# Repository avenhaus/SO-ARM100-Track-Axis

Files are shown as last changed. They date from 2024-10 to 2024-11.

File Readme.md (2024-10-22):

# <center>SO-ARM100 Track Axis</center>

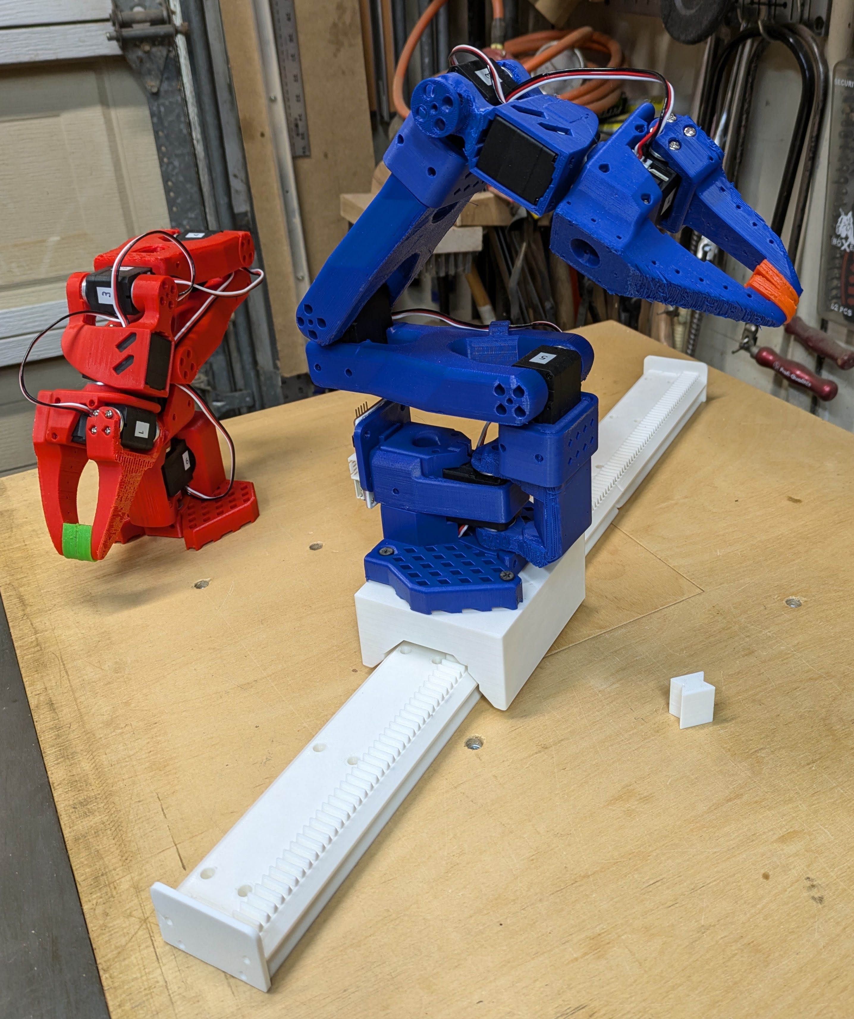
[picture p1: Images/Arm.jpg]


## Summary
This project is related to the [SO-ARM100](https://github.com/TheRobotStudio/SO-ARM100) robot arm and [LeRobot](https://github.com/huggingface/lerobot)

It provides an additional axis, using the same STS3215 servo.

The carriage comes in 2 Versions:
1) Direct Drive (best for leader with [encoders](https://github.com/avenhaus/SO-ARM100-Encoders) or higher precision)
2) Additional gear for twice the speed

## Hardware

- 1 x FeeTech STS3215 Servo (same as SO-ARM100)
- 8 x 624 Bearing (ID: 4mm / OD: 13mm / H: 5mm)
- 8 x M4 10mm or 12mm machine screws for bearings
- 6 x M3 6mm or 8mm screws for motor bracket
- 4 x M4 20mm bolts and hex nuts to mount arm to slide (there are also versions with 3.2mm holes for drywall screws)
- M3 wood screws to mount rails to wooden base

The "Fast" version with additional gear additionally needs: 
- 2 x 624 Bearing (ID: 4mm / OD: 13mm / H: 5mm)
- 1 x 4mm rod, ca. 35mm, longer is fine

### Drive Gear Specs

- Modulo: 1.5
- Pressure Angle: 20
- 18 Teeth
- Height: 14mm 

## Code

The servo can give current feedback. This is used to home the axis and find the length of the track. A small python program demonstrates this and also shows how to keep track of multiple servo rotations.

- Find end of track
- Find home position
- Move to 10% and 90% of track length
- Move to middle

## Video

**https://youtu.be/PuqxYcexV3M**

## Images

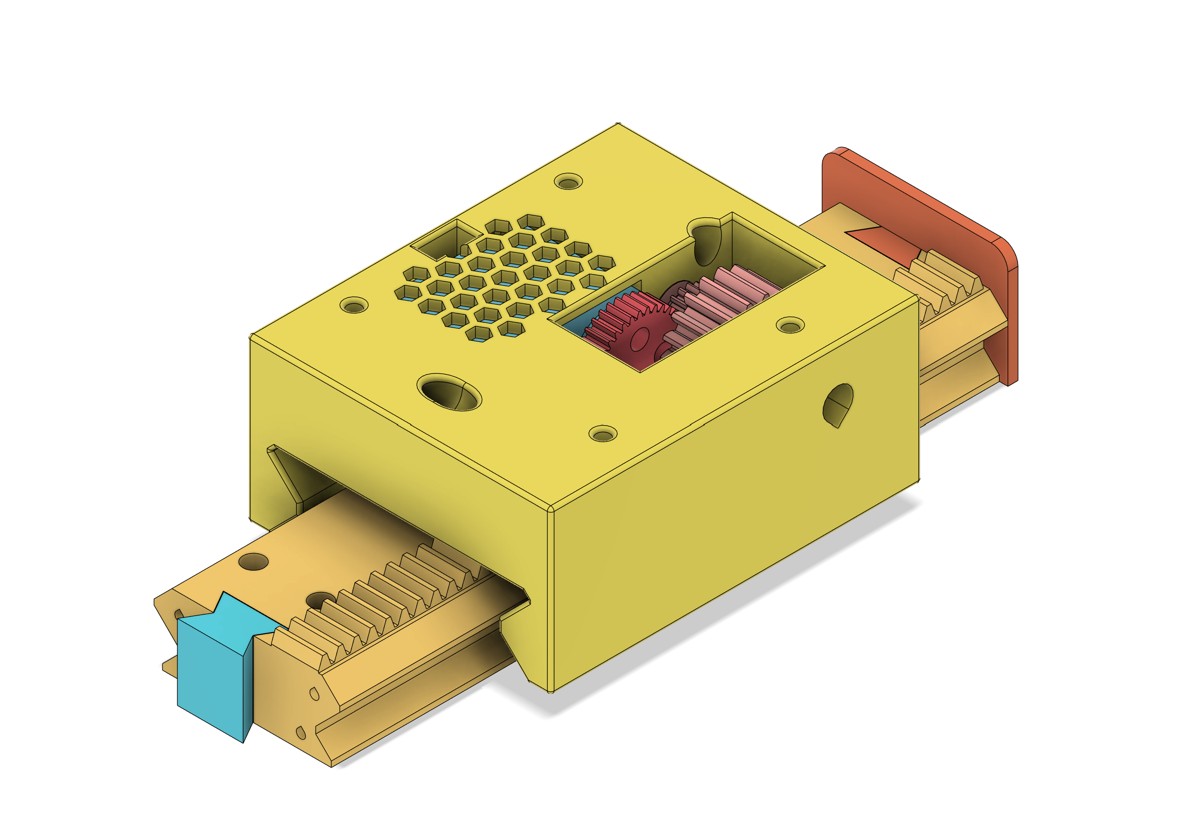
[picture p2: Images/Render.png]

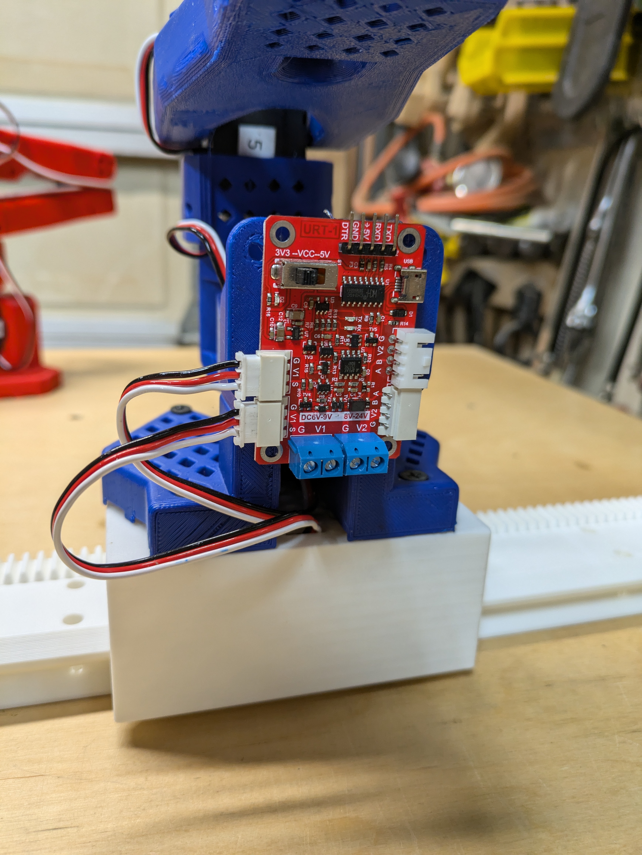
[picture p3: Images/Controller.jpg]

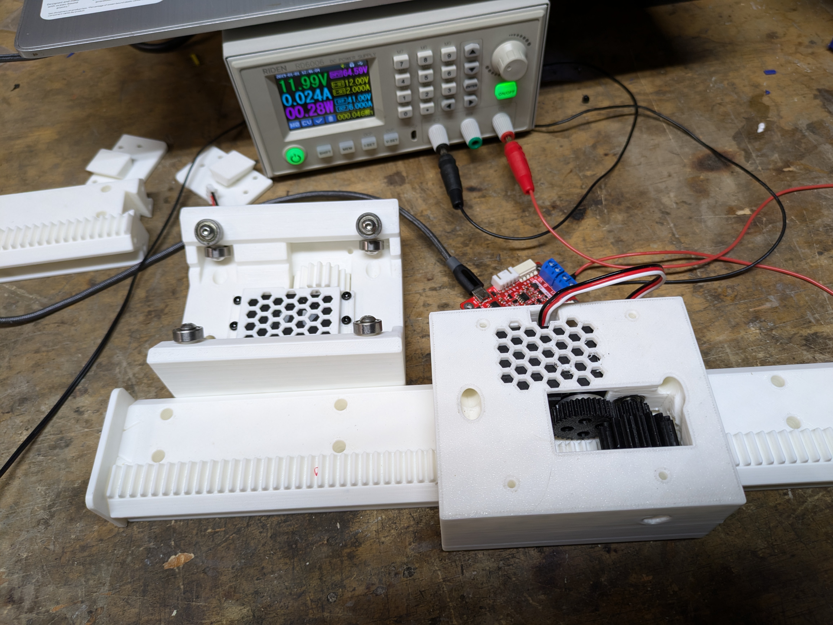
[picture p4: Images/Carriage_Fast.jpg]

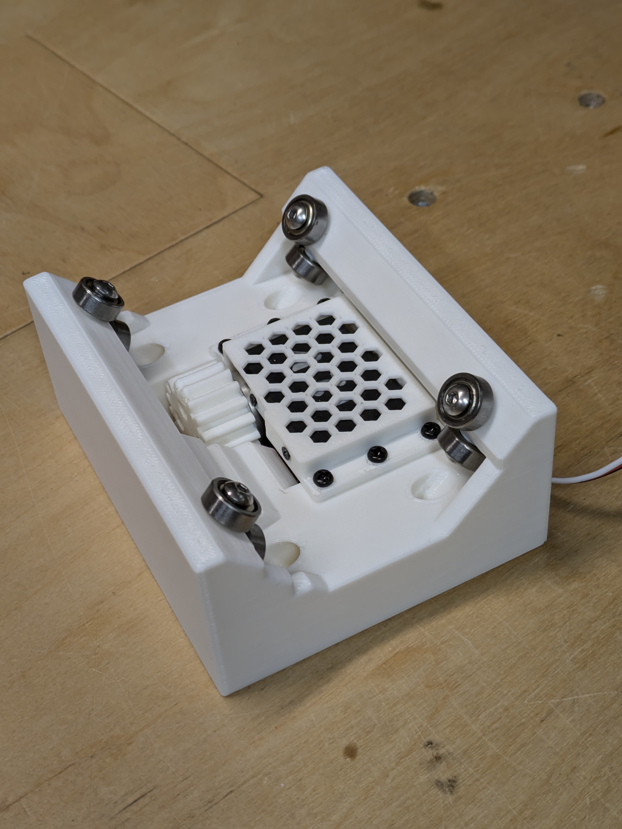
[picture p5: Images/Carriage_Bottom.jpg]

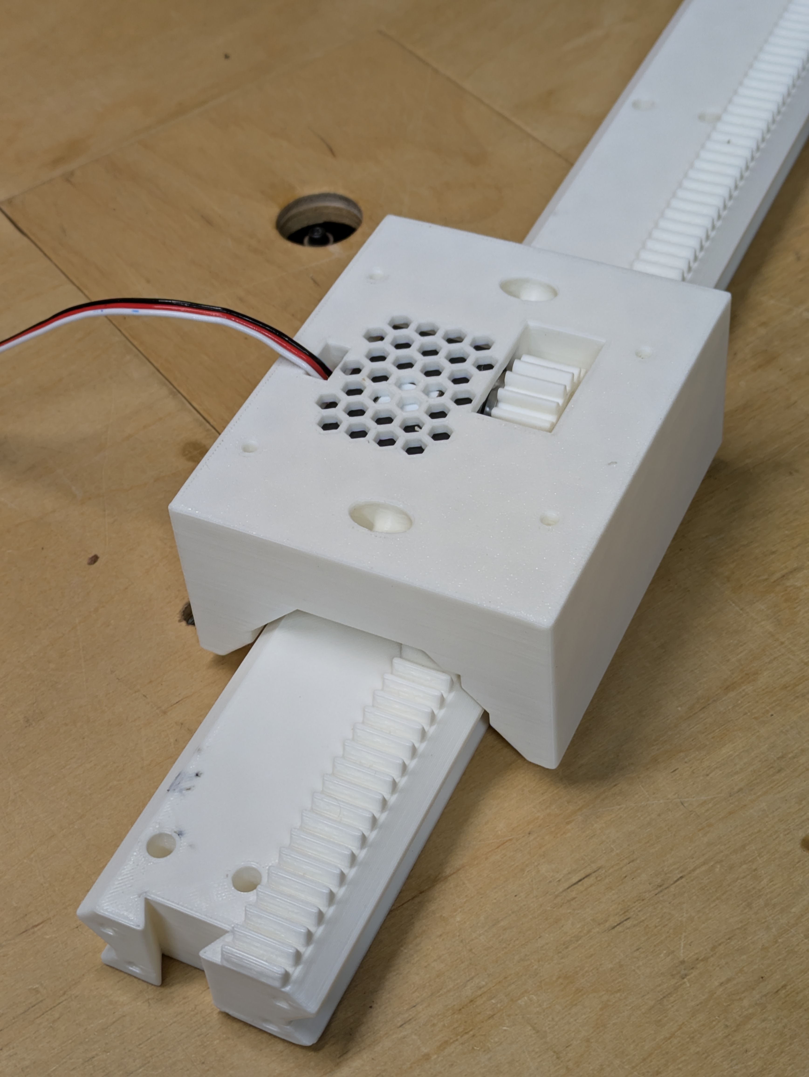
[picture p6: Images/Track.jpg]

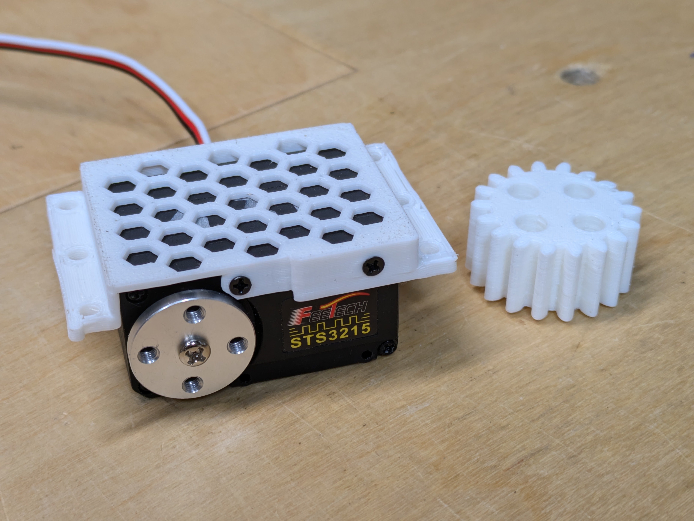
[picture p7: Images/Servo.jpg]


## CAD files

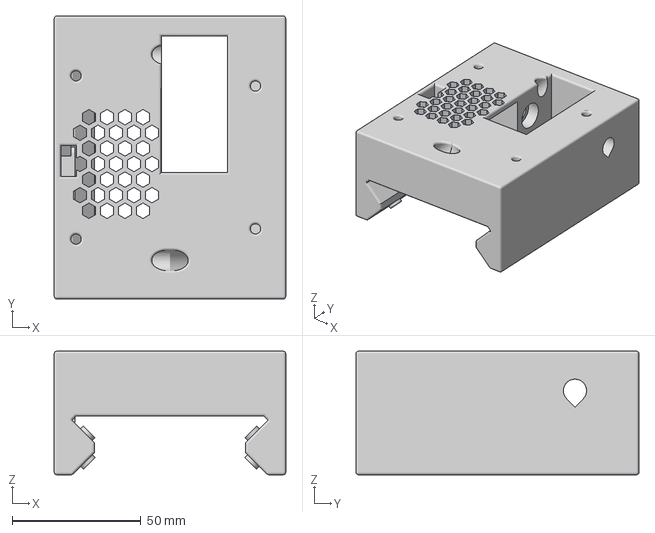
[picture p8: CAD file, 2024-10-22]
Parts/Carriage Fast M4 Mounts.3mf
90.0 x 110.0 x 48.0 mm

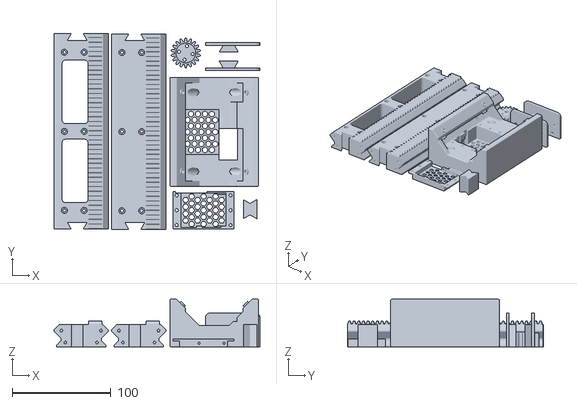
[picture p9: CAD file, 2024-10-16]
SO-ARM100_7th_Axis.stl
208.4 x 198.3 x 48.0

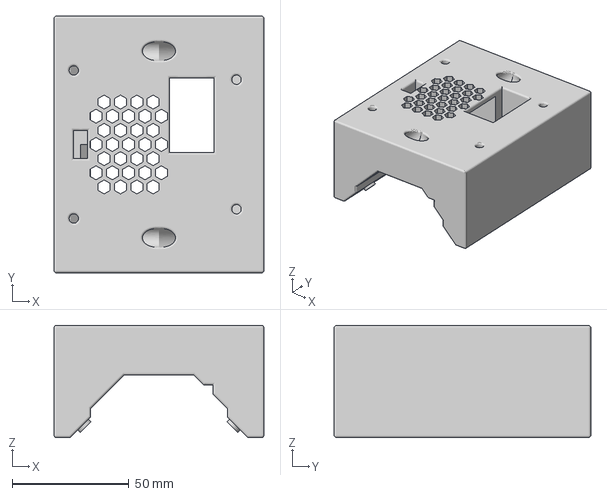
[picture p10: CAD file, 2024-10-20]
Parts/Carriage Slow M4 Mounts.3mf
90.0 x 110.0 x 48.0 mm

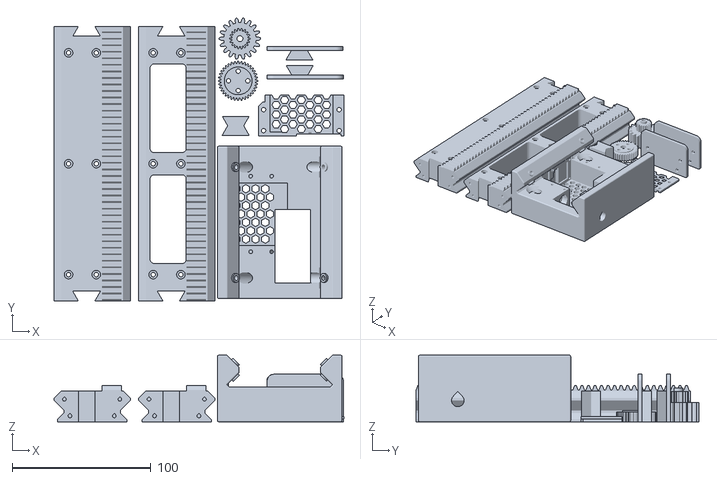
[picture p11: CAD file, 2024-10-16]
SO-ARM100_7th_Axis_Fast.stl
209.2 x 204.0 x 48.0

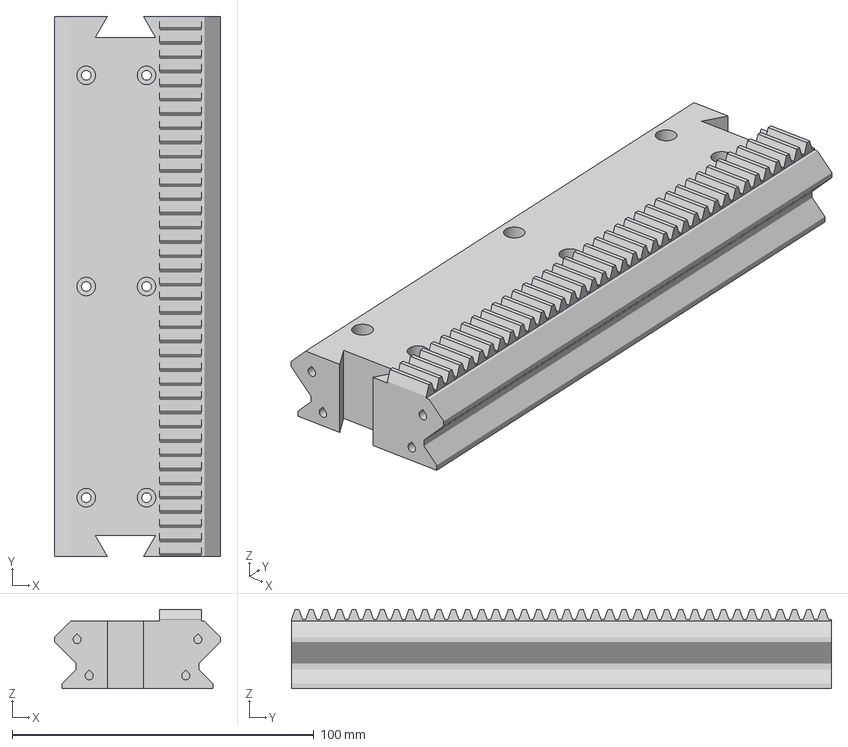
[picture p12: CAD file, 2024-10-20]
Parts/Track 179mm.3mf
55.0 x 179.1 x 26.2 mm

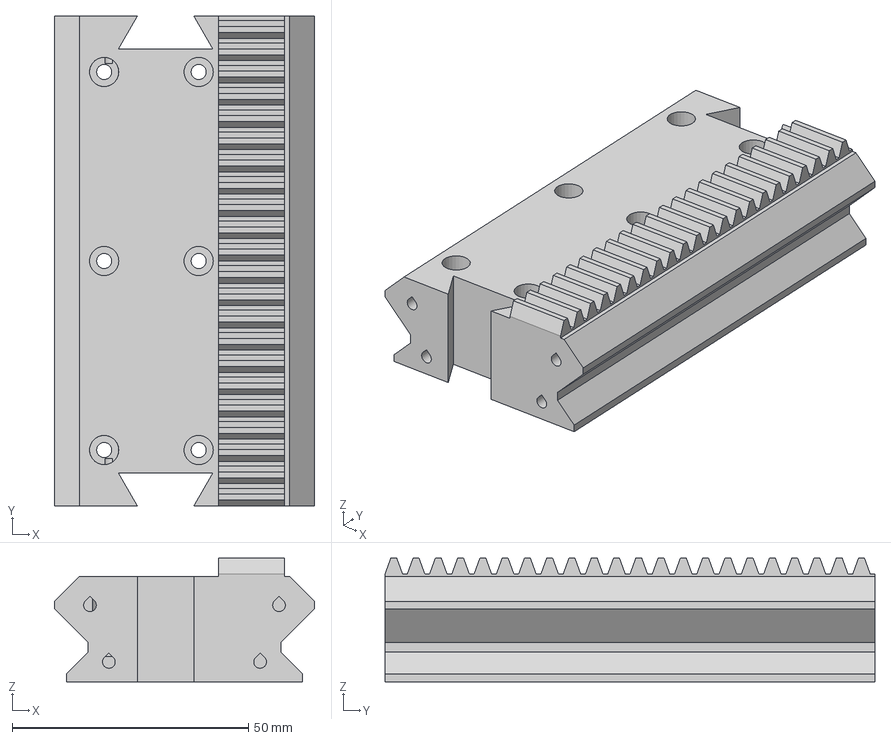
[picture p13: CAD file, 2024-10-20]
Parts/Track 103mm.3mf
55.0 x 103.7 x 26.2 mm

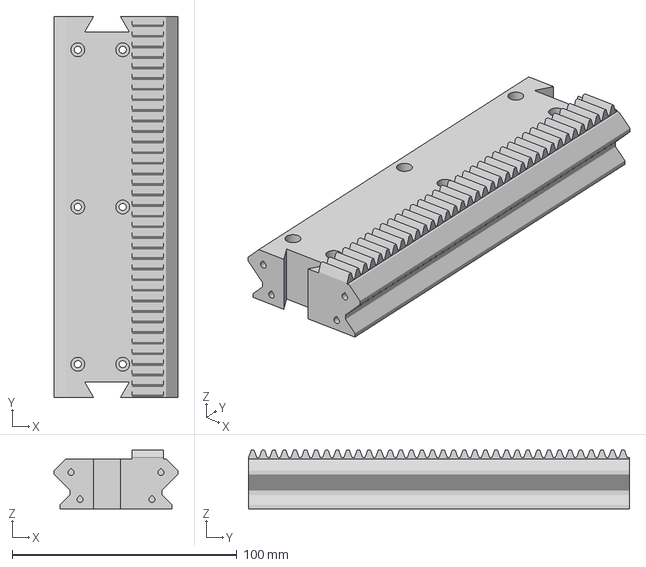
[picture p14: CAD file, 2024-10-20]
Parts/Track 170mm.3mf
55.0 x 169.6 x 26.2 mm

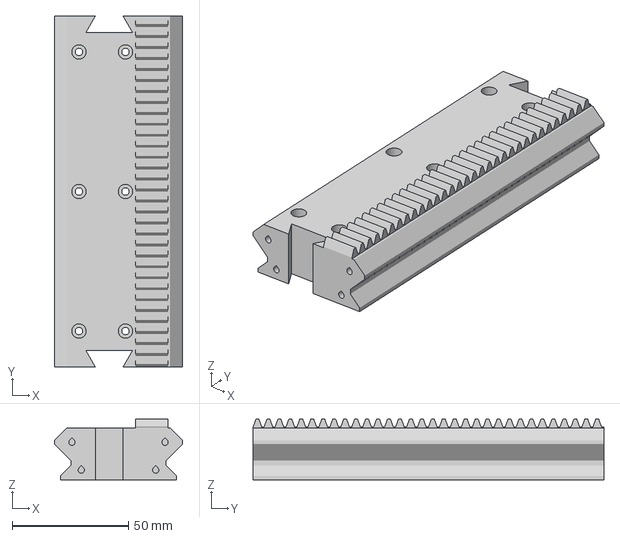
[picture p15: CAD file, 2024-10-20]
Parts/Track 150mm.3mf
55.0 x 150.8 x 26.2 mm

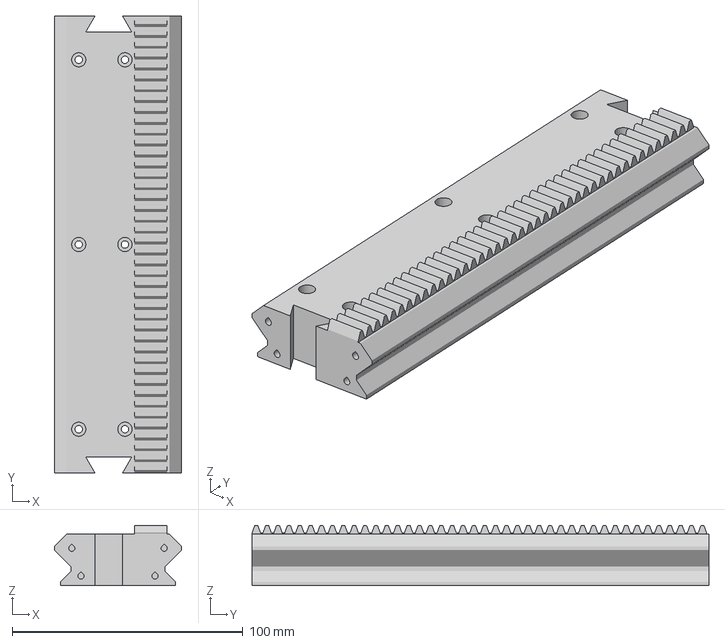
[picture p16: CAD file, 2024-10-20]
Parts/Track 198mm.3mf
55.0 x 197.9 x 26.2 mm

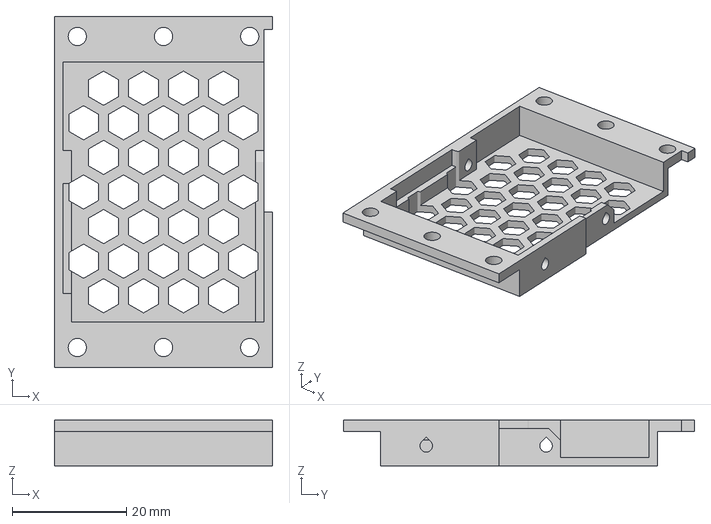
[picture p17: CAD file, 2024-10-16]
Parts/Bracket Slow.3mf
38.2 x 61.5 x 8.00 mm

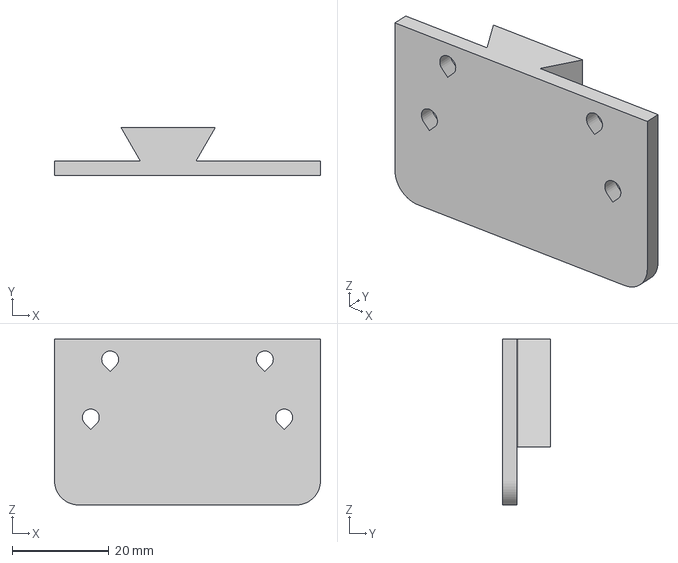
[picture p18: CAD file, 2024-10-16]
Parts/Stop_R.3mf
55.0 x 9.85 x 34.3 mm

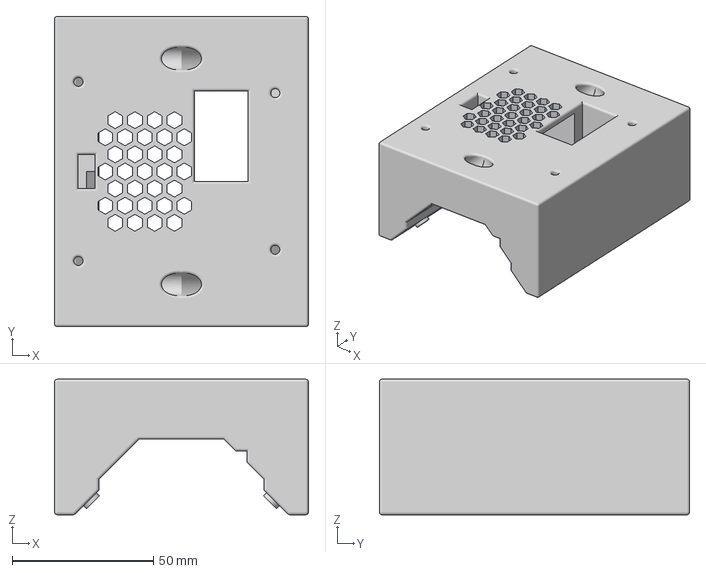
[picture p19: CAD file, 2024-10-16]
Parts/Body Slow Drywall Mounts.3mf
90.0 x 110.0 x 48.0 mm

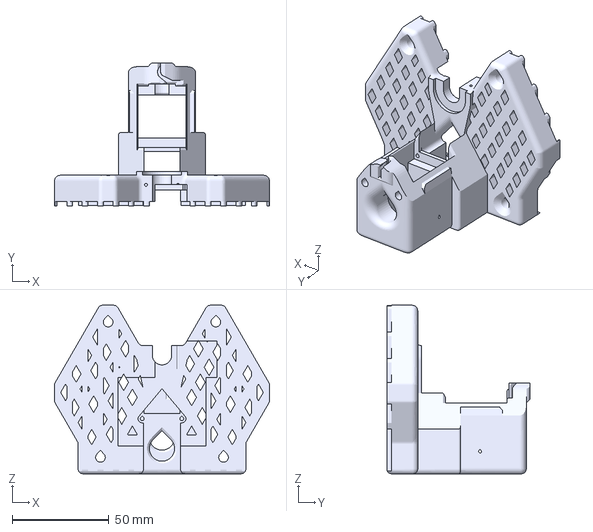
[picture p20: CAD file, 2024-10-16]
Parts/Base_08q v2.3mf
110.9 x 74.0 x 87.0 mm

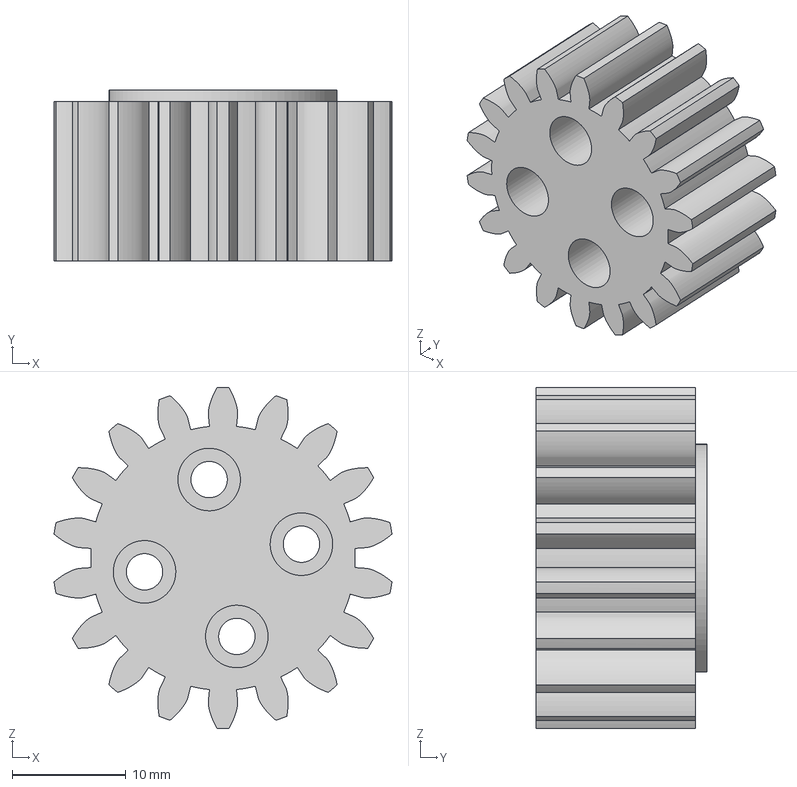
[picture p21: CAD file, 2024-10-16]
Parts/Gear Slow Mod 1.5.3mf
29.7 x 15.0 x 30.0 mm

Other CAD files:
Parts/Stop_L.3mf
Parts/Gear Fast Mod 0.75.3mf
Parts/Track.3mf
Parts/Gear Fast Mod 0.75 36T.3mf
Parts/Body Low.3mf
Parts/Bracket Fast.3mf
Parts/Carriage Fast Drywall Mounts.3mf
Parts/Connector.3mf

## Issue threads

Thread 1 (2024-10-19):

Feature request: Smaller tracks for Prusa Mini

adityakamath, 2024-10-19:
It would be awesome if you could provide smaller track parts so that I can print them on my Prusa Mini. The bed size is 18x18cm, so maybe a 16cm long track would be perfect! Thanks!

PS: The other parts can be printed on the Prusa Mini, and they are really well designed, great job! :D

adityakamath, 2024-10-19:
Btw, I managed to make it shorter by cutting a section off the fusion360 model, it would be nice to have an official version for future users. :)

avenhaus, 2024-10-19:
Great! I will look into it. Did you try orienting 45 degrees?

On Sat, Oct 19, 2024 at 5:03 AM Aditya Kamath ***@***.***>
wrote:

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

adityakamath, 2024-10-19:
Yes, still didn't fit. I removed 6 teeth to get it to size, and still had to turn 45 degrees on the slicer.

Btw I will be away from my laptop for a week, but when I'm back I can make a PR with the shorter track 3mf file.

avenhaus, 2024-10-19:
Great, thank you.

On Sat, Oct 19, 2024 at 12:38 PM Aditya Kamath ***@***.***>
wrote:

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

avenhaus, 2024-10-20:
I added a bunch of different track lengths and also made carriage versions with M4 mounts instead of the somewhat non stadard 3.2mm drywall screw holes.

I have not tested the M4 mounts. If you do please let me know.

adityakamath, 2024-10-27:
Awesome! I already printed the carriage and used 3.2mm drywall screws, which worked perfectly! I have an intern who might be making one in a few months, I'll ask her to check out the M4 mount option..

Closed 2024-10-20.

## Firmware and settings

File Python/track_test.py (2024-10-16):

#!/usr/bin/env python
#
# *********    Track Test     *********
#
# Find the track end and home the track servo
# Then move to some positions relative to the track length
#
# Needs FeeTech Servo SDK library to be installed:
# https://github.com/Adam-Software/Feetech-Servo-SDK
# pip install feetech-servo-sdk

import os
from time import sleep
from scservo_sdk import *                    # Uses SCServo SDK library

# Control table address
SCS_MIN_POS_LIMIT     = [ 9, 2, "Min Position Limit"]
SCS_MAX_POS_LIMIT     = [11, 2, "Max Position Limit"]
SCS_POS_CORRECTION    = [31, 2, "Position Correction"]
SCS_WORK_MODE         = [33, 1, "Work Mode"]
SCS_TORQUE_ENABLE     = [40, 1, "Torque Enable"]
SCS_GOAL_ACC          = [41, 2, "Goal Acceleration"]
SCS_GOAL_POSITION     = [42, 2, "Goal Position"]
SCS_GOAL_SPEED        = [46, 2, "Goal Speed"]
SCS_TORQUE_LIMIT      = [48, 2, "Torque Limit"]
SCS_LOCK_FLAG         = [55, 1, "Lock Flag"]
SCS_PRESENT_POSITION  = [56, 2, "Present Position"]
SCS_PRESENT_VELOCITY  = [58, 2, "Present Velocity"]
SCS_PRESENT_LOAD      = [60, 2, "Present Load"]
SCS_PRESENT_CURRENT   = [69, 2, "Present Current"]
SCS_UNDOCUMENTED_MAGIC= [85, 1, "Undocumented MAGIC"]

# Default setting
SCS_ID                      = 1                 # SCServo ID : 1
BAUDRATE                    = 1000000           # SCServo default baudrate : 1000000
DEVICENAME                  = 'COM3'    # Check which port is being used on your controller
                                                # ex) Windows: "COM1"   Linux: "/dev/ttyUSB0" Mac: "/dev/tty.usbserial-*"
protocol_end                = 0           # SCServo bit end(STS/SMS=0, SCS=1)


rotations = 0
track_min = 0
track_max = 0
range

# Initialize PortHandler instance
# Set the port path
# Get methods and members of PortHandlerLinux or PortHandlerWindows
portHandler = PortHandler(DEVICENAME)

# Initialize PacketHandler instance
# Get methods and members of Protocol
packetHandler = PacketHandler(protocol_end)

def init():
    # Open port
    if portHandler.openPort():
        print("Succeeded to open the port")
    else:
        print("Failed to open the port")
        quit()

    # Set port baudrate
    if portHandler.setBaudRate(BAUDRATE):
        print("Succeeded to change the baudrate")
    else:
        print("Failed to change the baudrate")
        quit()


def servo_set(ID, reg, value):
    # Write SCServo register
    if reg[1] == 1:
        scs_comm_result, scs_error = packetHandler.write1ByteTxRx(portHandler, ID, reg[0], value)   
    else:
        scs_comm_result, scs_error = packetHandler.write2ByteTxRx(portHandler, ID, reg[0], SCS_TOSCS(value,15))
    if scs_comm_result != COMM_SUCCESS:
        print(f"Servo {ID} Set {reg[2]} {value}: {packetHandler.getTxRxResult(scs_comm_result)}")
    elif scs_error != 0:
        print(f"Servo {ID} Set {reg[2]} {value} error:{packetHandler.getRxPacketError(scs_error)}")

def servo_get(ID, reg):
    # Read SCServo register
    if reg[1] == 1:
        value, scs_comm_result, scs_error = packetHandler.read1ByteTxRx(portHandler, ID, reg[0])
    else:
        value, scs_comm_result, scs_error = packetHandler.read2ByteTxRx(portHandler, ID, reg[0])
        value = SCS_TOHOST(value, 15)
    if scs_comm_result != COMM_SUCCESS:
        print(f"Servo {ID} Get {reg[2]}: {packetHandler.getTxRxResult(scs_comm_result)}")
    elif scs_error != 0:
        print(f"Servo {ID} Get {reg[2]} error: {packetHandler.getRxPacketError(scs_error)}")
    return value

def check_servo_config(ID):
    # This speeds up servo movements
    v = servo_get(ID, SCS_UNDOCUMENTED_MAGIC)
    print(f"{ID}: Magic Config = {v}")
    if v!=250:
        print(f"{ID}: Enabling Magic 250. Default is 50")
        servo_set(ID, SCS_LOCK_FLAG, 0)
        servo_set(ID, SCS_UNDOCUMENTED_MAGIC, 250)
        servo_set(ID, SCS_LOCK_FLAG, 1)


def get_current_position(ID):
    # Read SCServo present position
    scs_present_position_speed, scs_comm_result, scs_error = packetHandler.read4ByteTxRx(portHandler, ID, SCS_PRESENT_POSITION[0])
    if scs_comm_result != COMM_SUCCESS:
        print(f"Servo {ID} Get Current: {packetHandler.getTxRxResult(scs_comm_result)}")
    elif scs_error != 0:
        print(f"Servo {ID} Get Current error: {packetHandler.getRxPacketError(scs_error)}")

    scs_present_position = SCS_LOWORD(scs_present_position_speed)
    scs_present_speed = SCS_HIWORD(scs_present_position_speed)
    return scs_present_position, scs_present_speed        

def find_end(ID, speed):
    global rotations
    print(f"Current Position: {servo_get(ID, SCS_PRESENT_POSITION)}")
    servo_set(ID, SCS_GOAL_SPEED, speed)
    print(f"Current Position: {servo_get(ID, SCS_PRESENT_POSITION)}")
    print(f"Goal Speed: {servo_get(ID, SCS_GOAL_SPEED)}")   
    servo_set(SCS_ID, SCS_TORQUE_ENABLE, 1) # Enable servo
    print(f"Current Position: {servo_get(ID, SCS_PRESENT_POSITION)}")

    current = 0
    old_pos = servo_get(ID, SCS_PRESENT_POSITION)
    pos, speed = get_current_position(ID)
    if old_pos < 1000 and pos > 3000: # Underflow
        rotations -= 1
    if old_pos > 3000 and pos < 1000: # Overflow
        rotations += 1
    track_pos = pos + 4096 * rotations
    print(f"ID:{ID} servo pos:{pos} rotations:{rotations} track pos:{track_pos} speed:{SCS_TOHOST(speed, 15)} old pos:{old_pos}")

    while abs(current) < 15:
        pos, speed = get_current_position(ID)
        if old_pos < 1000 and pos > 3000: # Underflow
            rotations -= 1
        if old_pos > 3000 and pos < 1000: # Overflow
            rotations += 1
        old_pos = pos
        load = servo_get(ID, SCS_PRESENT_LOAD)
        current = servo_get(ID, SCS_PRESENT_CURRENT)
        track_pos = pos + 4096 * rotations
        # print(f"ID:{ID} servo pos:{pos} rotations:{rotations} track pos:{track_pos} speed:{SCS_TOHOST(speed, 15)} load:{load}, current:{current}")
        if rotations < -7:
            print("Turns exceeded, Could not find home position")
            quit()
    servo_set(ID, SCS_GOAL_SPEED, 0)
    servo_set(SCS_ID, SCS_TORQUE_ENABLE, 0) # Disable servo
    sleep(0.1) # Wait for servo to stop

    pos, speed = get_current_position(ID)
    if old_pos < 1000 and pos > 3000: # Underflow
        rotations -= 1
    if old_pos > 3000 and pos < 1000: # Overflow
        rotations += 1
    track_pos = pos + 4096 * rotations
    print(f"ID:{ID} servo pos:{pos} rotations:{rotations} track pos:{track_pos} speed:{SCS_TOHOST(speed, 15)})")

    return track_pos
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

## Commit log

2024-10-20 added different track lenghts and M4 mounting options
    [Body Slow Drywall Mounts.3mf, Body Tall.3mf, Bracket Slow.3mf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]
2024-10-20 M4 nut inserts from bottom
    [Carriage Fast M4 Mounts.3mf, Carriage Slow M4 Mounts.3mf, Gear Fast Mod 0.75 36T.3mf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]
2024-10-22 Moved servo = gears to fix interference with M4 nut
    [Carriage Fast M4 Mounts.3mf]
2024-11-03 Added Fusion 360 CAD export
